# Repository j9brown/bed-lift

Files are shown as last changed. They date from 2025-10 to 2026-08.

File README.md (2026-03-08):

# Bed-lift controller

Controls a motorized bed-lift with two synchronized linear actuators for vertical lifting and lowering and two pairs of synchronized stepper motors for horizontal extension and retraction.  It fits in the back of a campervan.

## Circuit board revisions

Refer to the following documents for design synopsis, schematics, and circuit board illustrations.

- [v1](./hardware/v1/design-and-errata.md): Fixed errata, improved assignment of pin functions, added span limit hall sensors, buzzer and ESD protection
- [v0.2](./hardware/v0.2/design-and-errata.md): First feature-complete circuit board
- [v0.1](./hardware/v0.1/design-and-errata.md): Initial hand-assembled prototype

## About the "forklift" bed

This custom motorized bed fits in the back of a small campervan to allow dual-use of the living area in a standard wheelbase vehicle.  In its raised position, the bed platform is only supported from the back which gives it the appearance of a pallet on a forklift, hence the name.

To maximize space efficiency, the bed is designed for sleeping crosswise with the head and feet towards the sides of the vehicle.  This choice of sleeping orientation poses unique engineering challenges; it is more common to design lifting beds for sleeping lengthwise with the head and feet towards the front and back of the vehicle.

Because the van is narrower at roof elevantion than at sleeping elevation, the bed extends and retracts to span the gap between the main body of the bed platform and the sides of the vehicle.  The parts that extend and retract are called the bed wings (aka. wing spans).  The bed mattress is made of three cushions: one large central cushion on the main body of the bed platform and two narrower cushions that rest on the two bed wings.  The narrower cushions are removed and stowed on top of the bed before retracting the bed wings.

- When the bed is raised, the bed wings retract into the bed platform and the platform is cantilevered from steel columns attached to the rear doorframe and floor of the vehicle.

- When the bed is lowered, the bed wings extend from the bed platform and rest upon reinforced windowsills to transfer the load of the occupants to the vehicle walls.

The bed has limited load bearing capacity while raised so it must be lowered when occupied or while driving to prevent excess torque through the cantilever.  As an advantage, there are no cables, straps, bulkheads, guides, posts, or other obstructions in the front of the living area to support the bed.  As a disadvantage, the bed structure is heavy and difficult to build.

Feel free to contact me for advice if you are interested in building a bed like mine (and be prepared for a challenge)!

[Video tour of the v0.2 prototype](https://vimeo.com/1154513482/b7c7d3c8f7)

<details>
<summary>Photos of v0.2 prototype</summary>

### Bed lift in lowered position viewed from outside
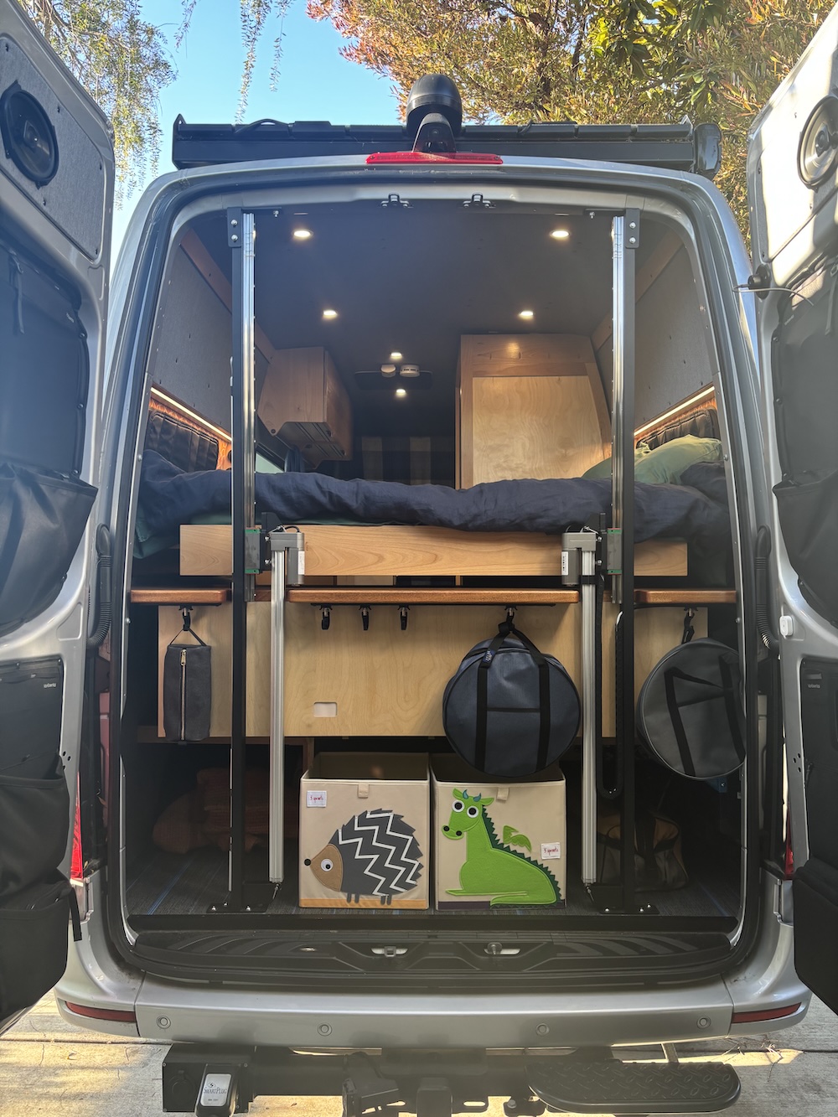
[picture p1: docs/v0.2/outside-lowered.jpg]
Bed lift in lowered position viewed from outside


### Bed lift in raised position viewed from outside
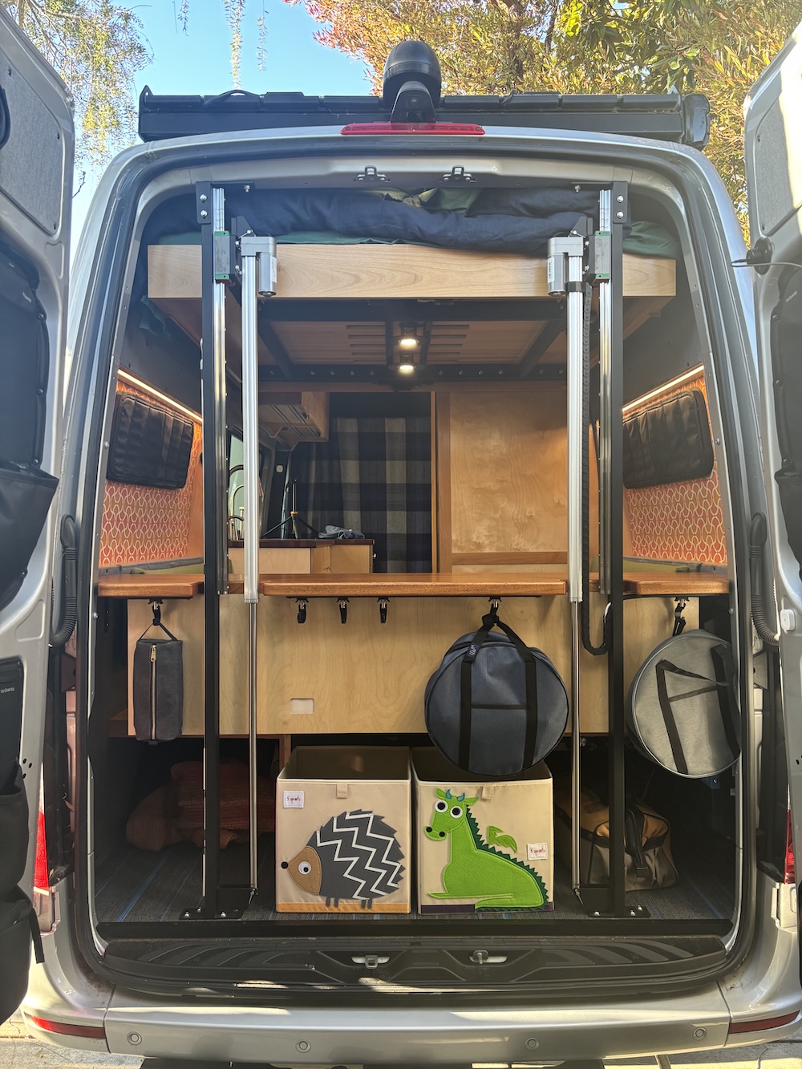
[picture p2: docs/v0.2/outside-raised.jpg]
Bed lift in raised position viewed from outside


### Bed lift in lowered position viewed from inside
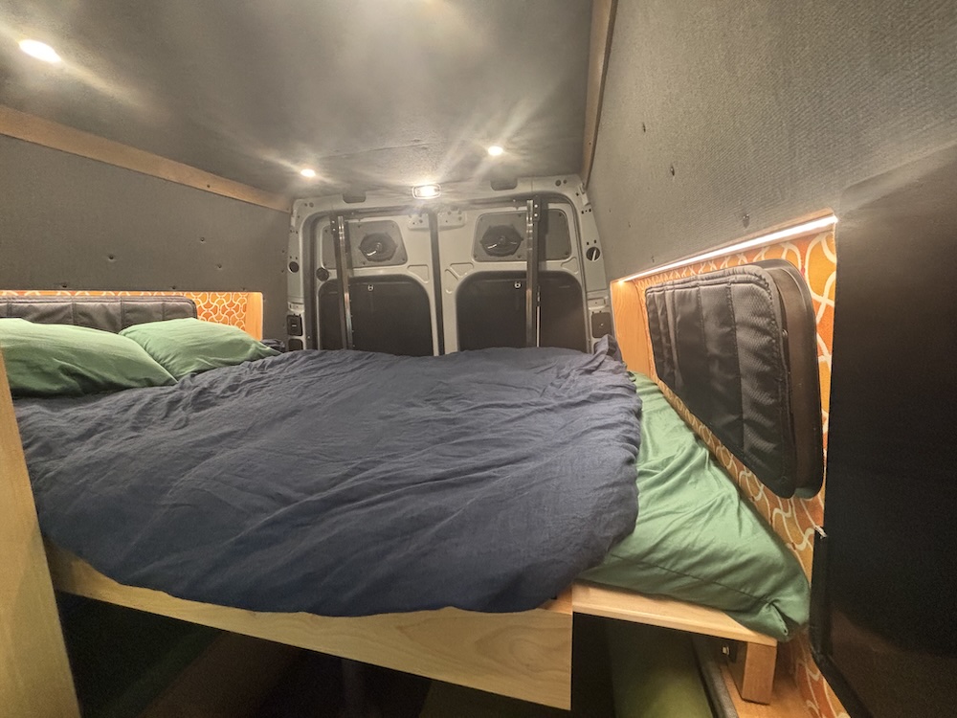
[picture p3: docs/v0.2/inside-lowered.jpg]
Bed lift in lowered position viewed from inside


### Bed lift in raised position viewed from inside
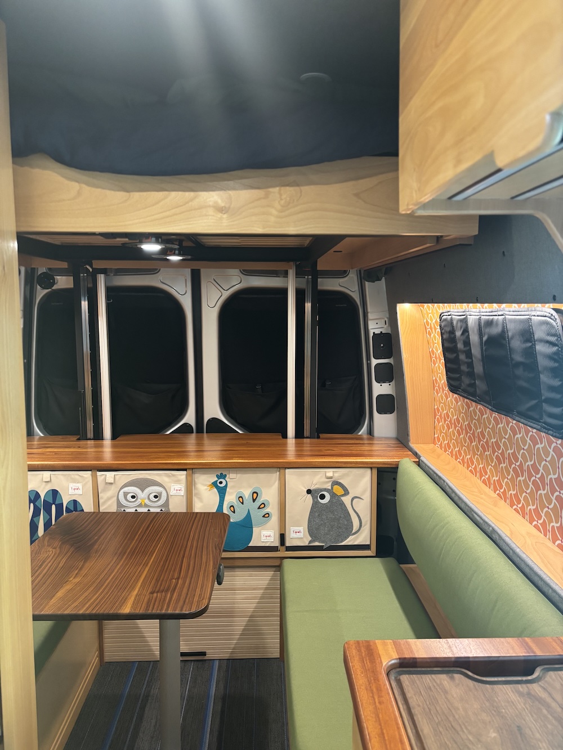
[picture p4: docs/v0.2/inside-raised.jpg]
Bed lift in raised position viewed from inside


### Bed lift controls
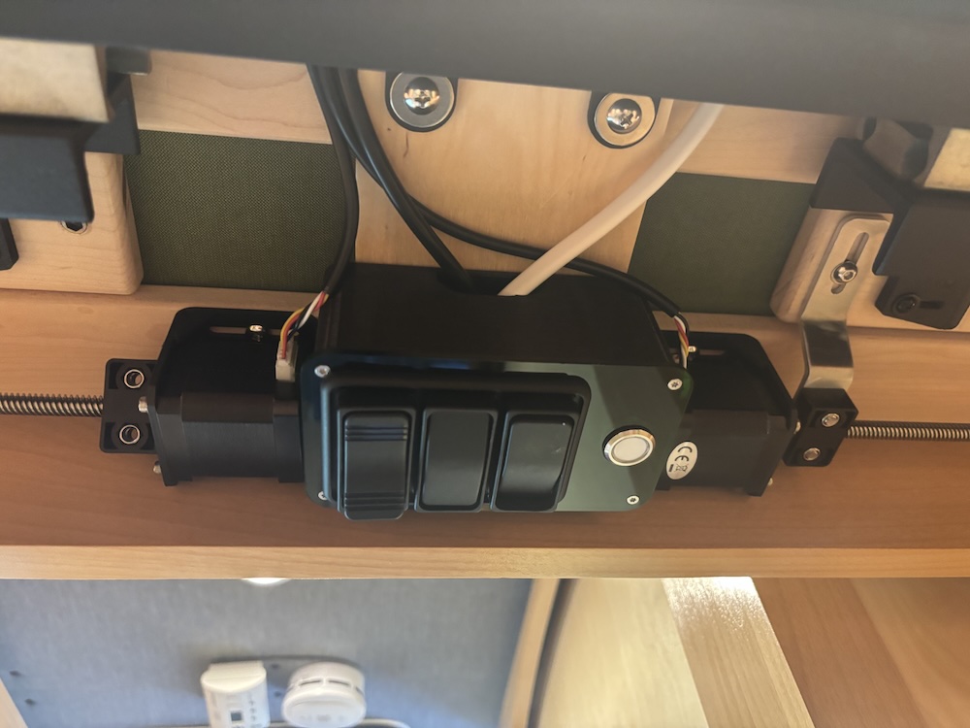
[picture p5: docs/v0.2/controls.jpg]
Bed lift controls


### Bed lift driver
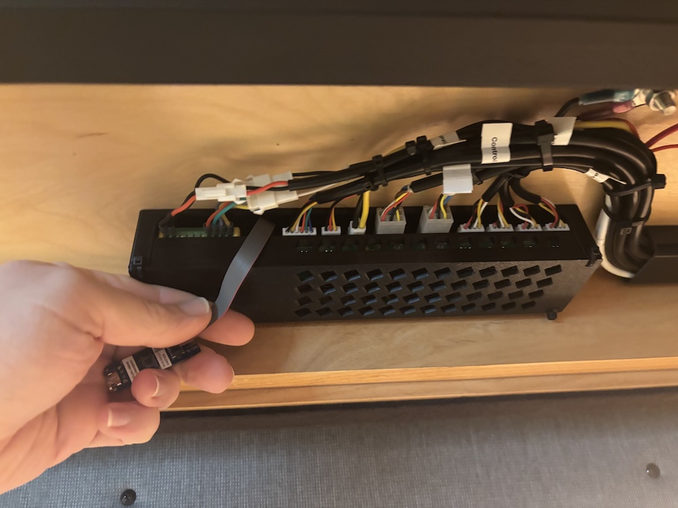
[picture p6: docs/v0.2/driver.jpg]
Bed lift driver


### Bed lift position encoder
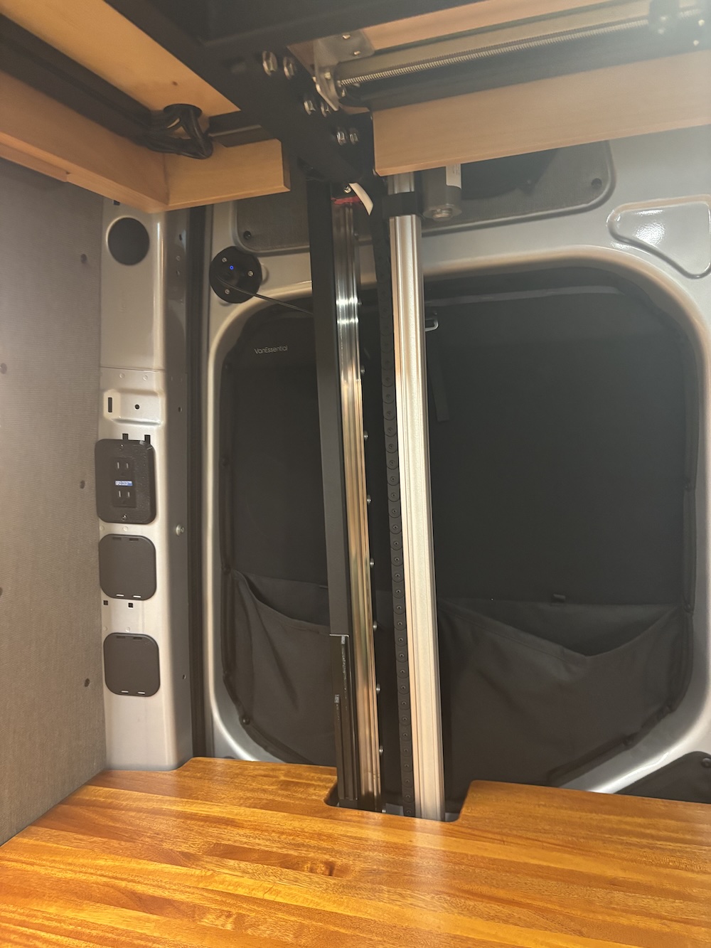
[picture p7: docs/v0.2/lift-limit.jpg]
Bed lift driver


</details>

<details>
<summary>Photos of v0.1 prototype</summary>

### Bed lift in lowered position
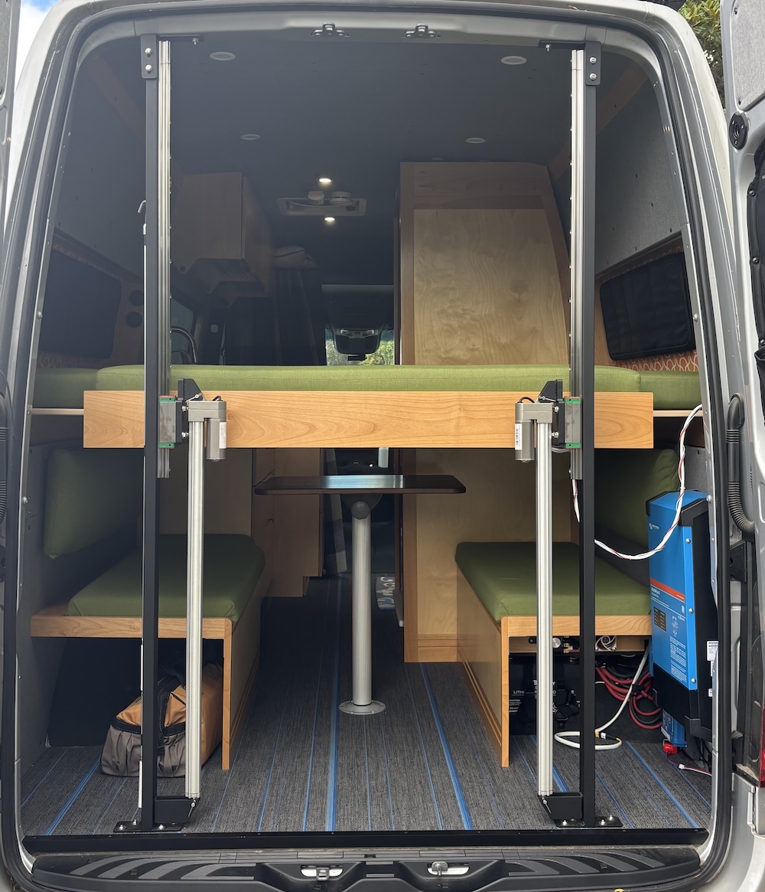
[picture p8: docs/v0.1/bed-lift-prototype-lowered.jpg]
Bed lift in lowered position


### Bed lift in raised position
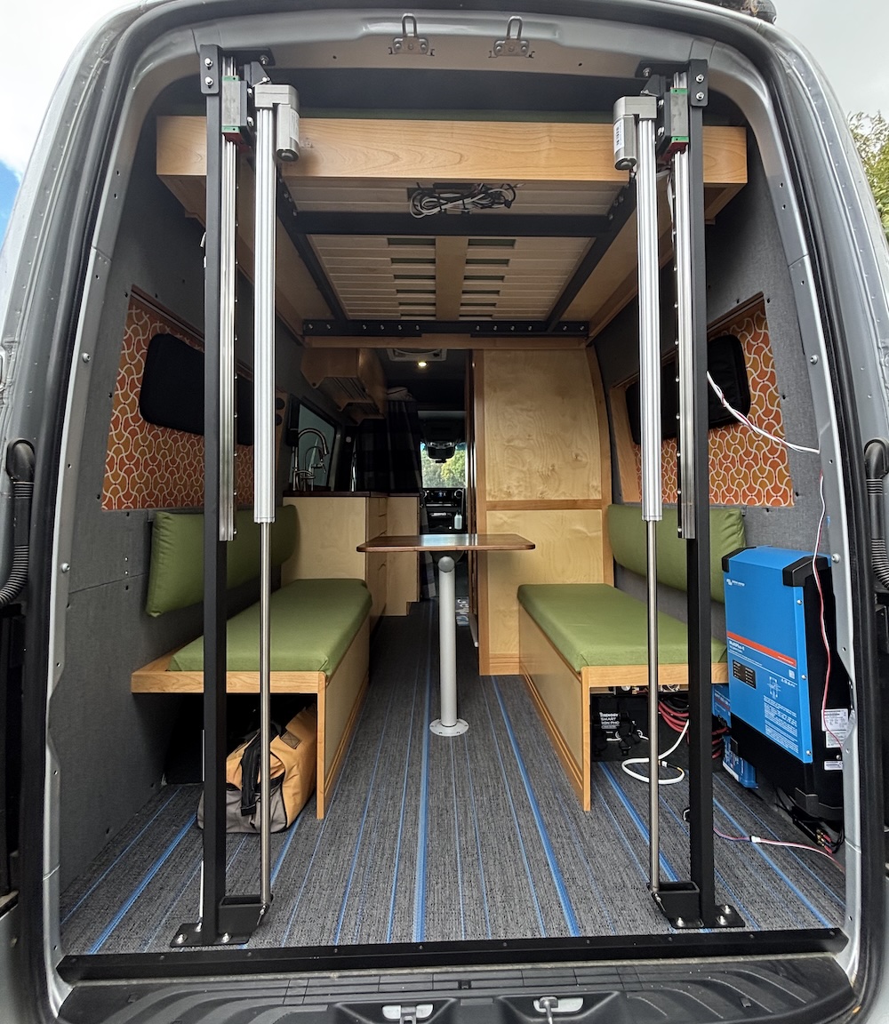
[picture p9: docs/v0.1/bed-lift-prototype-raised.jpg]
Bed lift in raised position


</details>

<details>
<summary>CAD model</summary>

### Bed lift in lowered position
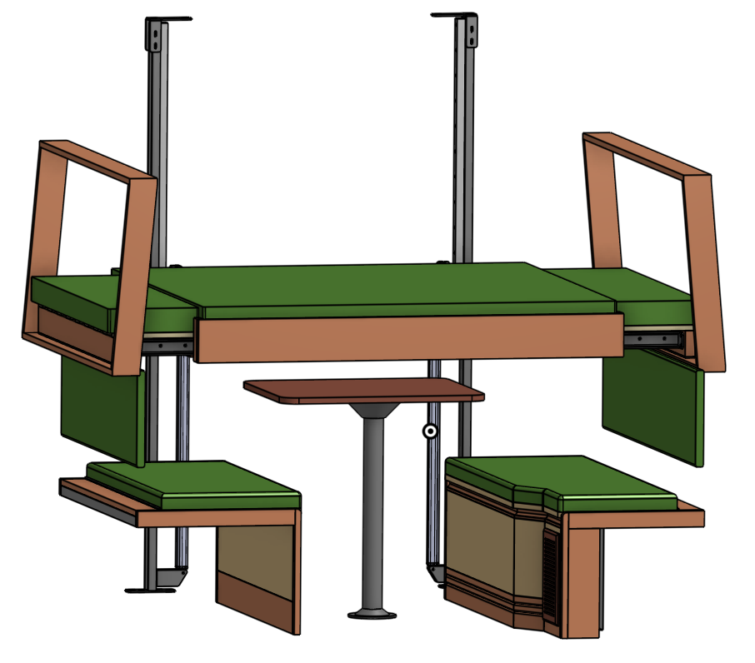
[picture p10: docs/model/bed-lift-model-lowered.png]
Bed lift in lowered position


### Bed lift in raised position
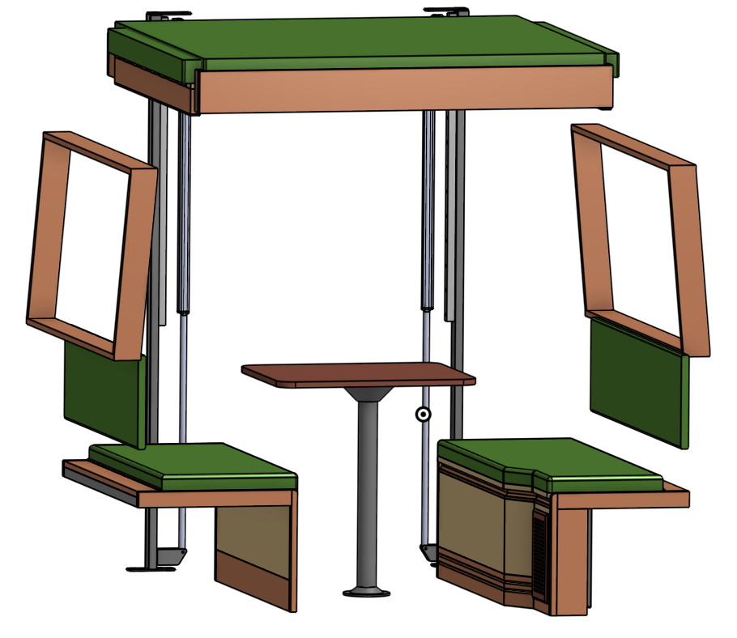
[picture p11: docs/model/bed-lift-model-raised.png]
Bed lift in raised position


</details>

## How to build the firmware

The firmware is based on Zephyr RTOS v4.3 and compiled with `west`.

1. Install the Zephyr RTOS SDK tools.  You can either follow the [Zephyr Getting Started Guide](https://docs.zephyrproject.org/latest/develop/getting_started/index.html) or install an extension for your IDE, such as [Zephyr IDE](https://zephyr-ide.mylonics.com/) or [Workbench for Zephyr](https://z-workbench.com/), that can install the tools for you.

2. Install the [xPack OpenOCD](https://xpack-dev-tools.github.io/openocd-xpack/docs/install/) package for your OS and add it to your system `PATH`.  This step is needed because the version of OpenOCD that is distributed with Zephyr is too old and doesn't support the STM32C0x series of chips.  We need OpenOCD v0.12.0-7 at minimum.

3. Get the code and its dependencies.  This is a little more complicated than simply cloning this git repository because the Zephyr `west` multi-tool assumes that all of the code resides within a top directory called a workspace.  You will need to create an empty directory to be the workspace first.  Here's how to do it from the command-line and the same thing can be done with IDE extensions.

```sh
$ mkdir bed-lift-workspace
$ cd bed-lift-workspace
$ west init -m https://github.com/j9brown/bed-lift
$ west update
```

4. Build and the firmware (either release or debug).

```sh
$ cd bed-lift/firmware/app
$ west build -p -d build/release
$ west build -p -d build/debug -- -DFEATURE_LOG=y -DFEATURE_DEBUG=y
```

5. Connect an ST-Link v3 programmer to the `DEBUG` port with an `STDC14` cable.  Flash the firmware.

```sh
$ cd bed-lift/firmware/app
$ west flash
```

Firmware for the older prototypes is preserved in the git history.

- The v0.2 firmware was based on Zephyr RTOS v4.2.1 and compiled with Platform IO.
- The v0.1 firmware was based on Arduino and compiled with Platform IO.

## Usage

The lift control panel has three switches:

- `Power`: This on / off switch provides power to the lift driver and all actuators.  It is intended to remain on indefinitely.  Can be used to cut power in case of emergencies.
- `Up / Off / Down`: This momentary-on / off / momentary-on switch has two positions.  Toggling the switch to the `Up` position raises the lift to the lounge position.  Toggling the switch to the `Down` position lowers the lift to the sleeping position.  The switch must be held in the `Up` or `Down` position for 0.5 seconds to engage the actuators as a precaution against accidental triggering.  The lift stops moving immediately as soon as the switch is released and returns to the `Off` position.
- `Mode`: This momentary-on / off switch activates special modes.

By default, the lift starts on the `Main Menu` and the `Up / Off / Down` controls whether the lift moves into the lounge or sleep position.

While holding the switch `Up` or `Down` and the lift is raising or lowering, press the `Mode` button to activate automatic movement.  Then, release all of the controls and the lift will continue moving in the requested direction until the final position is reached or an error occurs.  To stop automatic movement, press any control.

**Use caution when activating automatic movement and continue paying attention to the lift to avoid damage or injury!**

to ensure the lift won't encounter any obstructions in this mode because it could damage itself if you aren't paying attention!

To access a different menu, press and hold the `Mode` button for 3 seconds until the indicator lights `Amber` then blinks one or more times in a different color and a tone is played.  The second color indicates the menu and the number of blinks indicates the action that will be performed when the `Up / Off / Down` switch is activated.  Press the `Mode` button to cycle among actions and observe the number of blinks change.  Press and hold the `Mode` button for 0.5 seconds to access the next menu and observe the blink color change.  Refer to the table below to identify the currently selected menu action.

The lift reverts to an idle state when the user does not interact with the controls for some time.

### Visual feedback

An RGB color indicator shows the state of the device at the control panel.  There is also a monochromatic red LED on the circuit board itself that indicators the same state as the indicator (but without color).

- When the lift remains idle for some time, the indicator turns off.
- When the lift is rising, the indicator shows a rainbow color wheel cycling from red to violet.
- When the lift is lowering, the indicator shows a rainbow color wheel cycling from violet to red.
- When the lift achieves the lounge or sleep position, the indicator lights `Green`.
- When the lift movement is aborted without achieving the lounge or sleep position, the indicator lights `Amber`.
- When a diagnostic menu mode is active, the indicator lights `Amber` then blinks one or more times in a different color depending on the menu.
- When an error occurs, the indicator lights `Red` then blinks one or more times in a different color depending on the error.

| Solid color  | Blink color  | Blinks | Purpose  | Meaning |
| --- | --- | --- | --- | --- |
| Rainbow up | | | Activity | Lift is rising |
| Rainbow down | | | Activity | Lift is lowering |
| Green | | | Status | Lift is in lounge or sleep position, ready for use |
| Amber | | | Status | Lift is in an intermediate position, not ready for use |
| Amber | Cyan | 1 | Menu | Lift menu: Jog both lift actuators in tandem (synchronized) |
| Amber | Cyan | 2 | Menu | Lift menu: Jog both lift actuators indepedently (not synchronized) |
| Amber | Cyan | 3 | Menu | Lift menu: Jog lift actuator 1 (driver side) |
| Amber | Cyan | 4 | Menu | Lift menu: Jog lift actuator 2 (passenger side) |
| Amber | Blue | 1 | Menu | Span menu: Jog all span actuators in tandem (synchronized) |
| Amber | Blue | 2 | Menu | Span menu: Jog both span actuators 1 and 2 (driver side) in tandem (synchronized) |
| Amber | Blue | 3 | Menu | Span menu: Jog both span actuators 3 and 4 (passenger side) in tandem (synchronized) |
| Amber | Blue | 4 | Menu | Span menu: Jog both span actuator 1 (front driver side) independently (not synchronized) |
| Amber | Blue | 5 | Menu | Span menu: Jog both span actuator 2 (rear driver side) independently (not synchronized) |
| Amber | Blue | 6 | Menu | Span menu: Jog both span actuator 3 (front passenger side) independently (not synchronized) |
| Amber | Blue | 7 | Menu | Span menu: Jog both span actuator 4 (rear passenger side) independently (not synchronized) |
| Red | | | Error | Error: An unspecified error occurred |
| Red | Magenta | 1 | Error | Control error: Movement of the bed has been remotely inhibited |
| Red | Amber | 1 | Error | Bed error: The bed components are in an unknown or unexpected state |
| Red | Cyan | 1 | Error | Lift error: Motor driver reported a fault |
| Red | Cyan | 2 | Error | Lift error: The actuators lost synchronization |
| Red | Cyan | 3 | Error | Lift error: Lift stationary when it should be moving or the hall sensors are not working correctly |
| Red | Cyan | 1 | Error | Lift error: I/O error communicating with the motor driver |
| Red | Cyan | 1 | Error | Lift error: Operation timed out because poll wasn't called often enough |
| Red | Blue | 1 | Error | Span error: Motor driver reported a fault |
| Red | Blue | 2 | Error | Span error: The actuators lost synchronization |
| Red | Blue | 3 | Error | Span error: The actuators did not stall at their home position as expected |
| Red | Blue | 4 | Error | Span error: The actuators traveled further than the expected distance without stalling |
| Red | Blue | 5 | Error | Span error: I/O error communicating with the motor driver |
| Red | Blue | 6 | Error | Span error: Operation timed out because poll wasn't called often enough |

### Audible feedback

A piezo buzzer provides audible feedback.

- When the lift successfully raises into the lounge position, it plays a brief fanfare that ends on a rising tone.
- When the lift successfully lowers into the sleep position, it plays a brief fanfare that ends on a falling tone.
- When the lift encounters an error, it plays three long tones as an alert.
- When the user attempts to perform an action that has been remotely inhibited, the lift plays three quick tones.
- When using the diagnostic menu, the lift plays a tone as each menu or mode is entered.

### I2C interface

Connect an I2C host to the lift driver's `EXT I2C` port using a `QWIIC` connector to remotely monitor the device, remotely inhibit operation of the control panel, and access low-level debug and test features.  The `EXT I2C` port galvanically isolates the bed lift from the host's power supply for safety.

Refer to [monitor.c](./firmware/app/src/monitor.c) for the I2C protocol implementation.

## Notice

The bed-lift software, documentation, design, and all copyright protected artifacts are released under the terms of the [MIT license](LICENSE).

The bed-lift hardware is released under the terms of the [CERN-OHL-W license](hardware/LICENSE).

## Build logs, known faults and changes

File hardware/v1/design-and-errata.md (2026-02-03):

# Bed lift v1.0

**Status: Fabricated, tested, in service, no issues found**

## Design synopsis

The controller has the following major components:

- [STM32C051C8T6](https://www.st.com/resource/en/datasheet/stm32c051c8.pdf) with 64 KB flash and 12 KB RAM controls the actuators. It is programmed with SWD using a STDC14 connector. The timer peripherals are used extensively for motor control and feedback.
- [ISO1640](https://www.ti.com/lit/ds/symlink/iso1640.pdf) isolates the I2C bus to prevent ground loops through the `EXT I2C` connector because the driver has a separate power supply.
- Four [DRV8434S](https://www.ti.com/lit/ds/symlink/drv8434s.pdf) stepper motor drivers operate the four motors that extend and retract the side spans of the bed.
- Two [DRV8874](https://www.ti.com/lit/ds/slvsf66a/slvsf66a.pdf) motor drivers operate the two linear actuators that raise and lower the bed.
- [LP2985-33](http://www.ti.com/lit/ds/symlink/lp2985.pdf) LDO powers the logic circuits at 3.3 V
- [LP2985-50](http://www.ti.com/lit/ds/symlink/lp2985.pdf) LDO powers the hall sensors at 5.0 V
- [PS1240P02BT](https://product.tdk.com/en/system/files/dam/doc/product/sw_piezo/sw_piezo/piezo-buzzer/catalog/piezoelectronic_buzzer_ps_en.pdf) buzzer provides audible feedback
- Circuit protection elements
  - Supply: TVS
  - Actuators: overcurrent, stall-detection, open-load, short-circuit
  - Switch inputs: ESD diodes
  - External I2C bus: galvanic isolation, hot plug

The device receives user control input from a momentary rocker switch attached to the `CONTROL` input and it provides feedback on its progress with an RGB LED indicator and piezo buzzer. To synchronize the motors and move the bed lift into the correct pose, the device receives position feedback from the `LIFT` actuator hall sensors, `LIFT LIMIT` switches, `SPAN LIMIT` hall sensors, and stepper motor driver stall detection. It can also be monitored and controlled remotely by an external I2C host via the `EXT I2C` connector.

The `EXPANSION` and `INT I2C` interfaces expose additional signals for future use.

The circuit board requires a 12 V DC nominal supply protected by a 10 A external fuse.

The schematics include the BOM and metadata for the JLCPCB fabrication toolkit plug-in.

## Illustrations

[Schematics PDF](bed-lift.pdf)

### PCB front
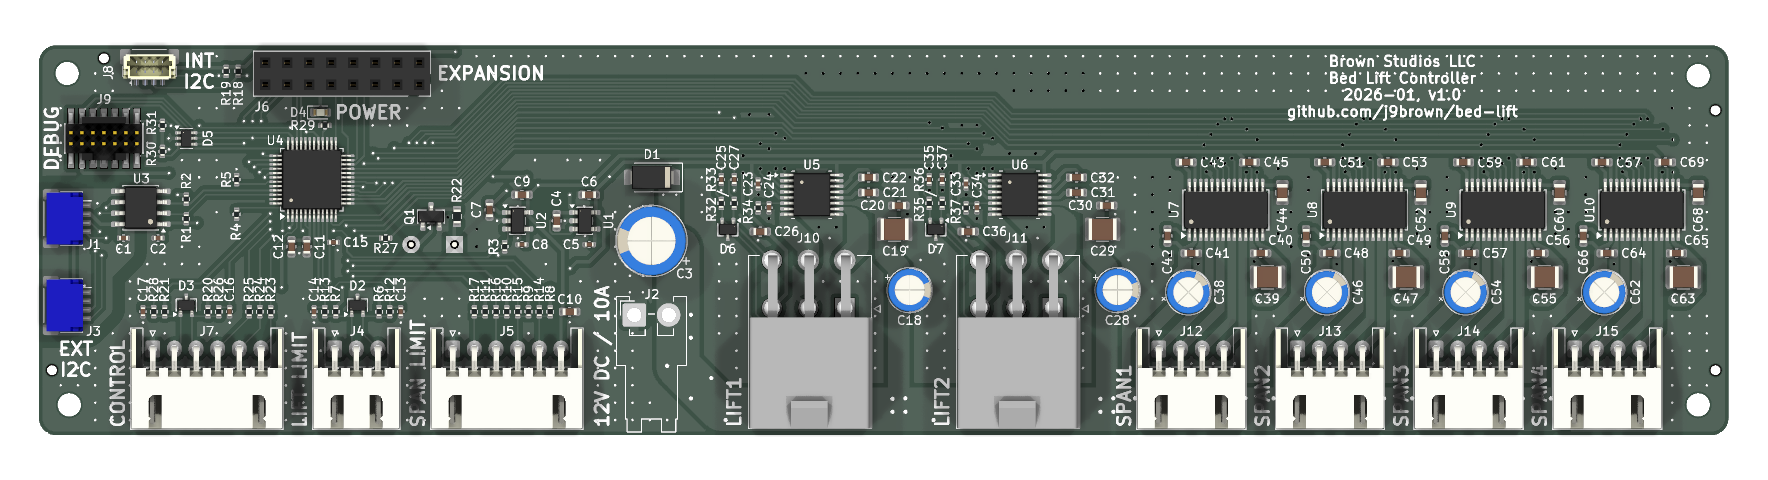
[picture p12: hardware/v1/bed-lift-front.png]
PCB front


### PCB back
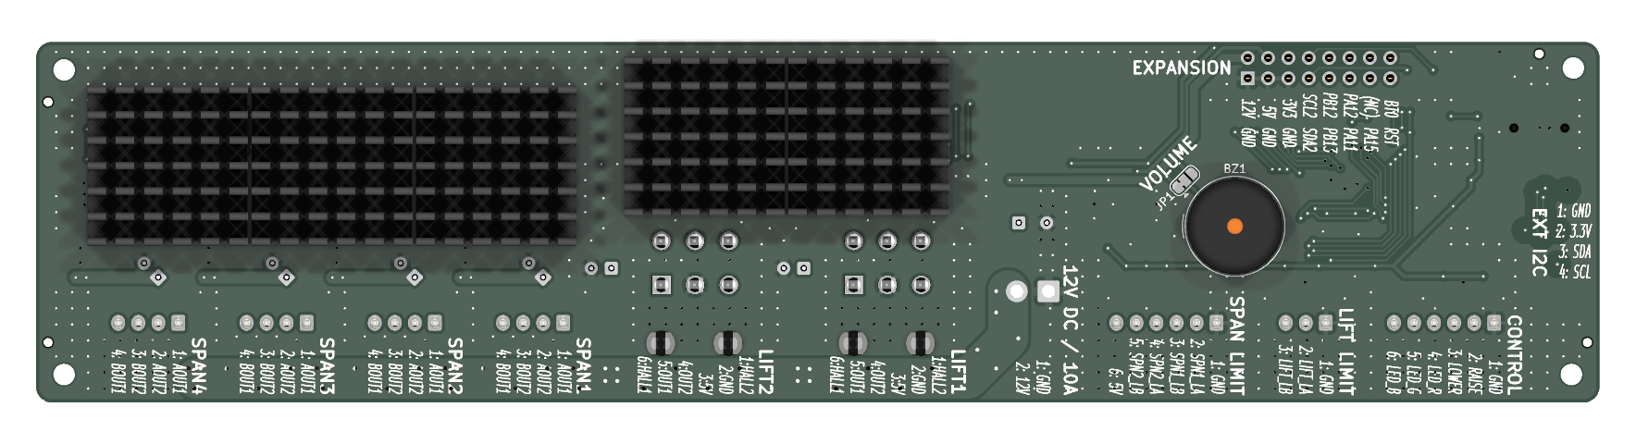
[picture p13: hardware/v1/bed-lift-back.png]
PCB back


## Fabrication

Use the `JLCPCB fabrication toolkit` plug-in to generate files for JLCPCB.

Fabrication parameters:

- Material: 4 layers, FR4 TG155, ENIG, 1 oz outer copper, 0.5 oz inner copper
- Via covering: plugged
- Min via hole size: 0.3 mm (default)
- Board outline tolerance: 0.2 mm (default)
- Assembly side: top
- Tooling holes: by customer
- Parts selection: by customer
- Solder paste: high temp (default)

Because the piezo buzzer is the only component on the back side, it may be cheaper to solder it manually after manufacture.

## Additional materials

Control panel switches

  - 3 gang switch panel mount
    - Carling Technologies VM3-01
  - Up/down control
    - Carling Technologies V8D2S001-00000-000 Contura momentary on/off/on rocker switch
    - Carling Technologies VVJZZ00-000 Contura XII paddle actuator
  - Mode control
    - Carling Technologies V2D2S001-00000-000 Contura momentary on/off rocker switch
    - Carling Technologies VV6ZZ00-000 Contura XI recessed actuator
  - Arm/disarm control
    - Carling Technologies V1D2S001-00000-000 Contura maintained on/off rocker switch
    - Carling Technologies VV1ZZ00-000 Contura X raised actuator
  - Generic small signal diodes to connect the mode switch to both up/down inputs

Control panel indicators

  - 3 V RGB panel indicator
    - Dialight 6251121307F or 6201121117F

Lift position encoders

  - 2 generic normally open lever arm micro limit switches with rollers

Span position encoders

  - 4 Littelfuse 55100-3M-02-A

Heat sinks

  - 5 generic 20 mm L x 20 mm W x 10 mm H self-adhesive heatsinks mounted on back side underneath the motor drivers

Actuators

  - 2 [Progressive Automation PA-09-03-30](https://www.progressiveautomations.com/products/mini-medium-force-linear-actuator) linear actuators for the lift, rated for 4 A peak at maximum 330 lbs load, hall sensor produces 660 pulses per inch of travel
  - 4 [Stepper Online 17E19S1684MB4-300RS](https://www.omc-stepperonline.com/nema-17-external-acme-linear-stepper-motor-1-68a-48mm-stack-screw-lead-8mm-0-31496-lead-length-300mm-17e19s1684mb4-300rs) stepper motors for the spans, rated for 1.68 A rms per phase

## Lift position encoders

Install two limit switches on the bed frame.  Each limit switch has a lever arm that is depressed when it rolls over a raised 3D printed plastic strip attached to the face of one of the bed lift columns.  Together the limit switches encode the position of the bed.

| State | Position | `Limit A` | `Limit B` | Wing action |
| ----- | --- | --- | --- | --- |
| `1` | Maximum elevation | `ON` | `OFF` | Fully retracted |
| `2` | Above safe zone | `OFF` | `OFF` | Fully retracted |
| `3` | Within safe zone | `OFF` | `ON` | Extending/retracting |
| `4` | Below safe zone | `ON` | `ON` | Fully extended |

To raise the bed...

  - state `4`: raise platform
  - state `3`: retract wings then raise platform (can do both simultaneously)
  - state `2`: retract wings then raise platform
  - state `1`:
    - if full range of travel permitted (no cushions or other bulky materials stored on the bed) then raise platform until end-of-travel
    - otherwise stop

To lower the bed...

  - state `1`: lower platform
  - state `2`: lower platform
  - state `3`: extend wings then lower platform (can do both simultaneously)
  - state `4`:
    - if wings fully extended then lower platform until end-of-travel
    - otherwise: raise platform until state `3` achieved and the wings can be extended

## Span hall sensors

Install one hall sensor at each of the end-of-travel of the rear span actuators on both sides for a total of 4 sensors.

Although end-of-travel can be determined by observing stepper motor stalls, the motor can stall in mid-travel when it encounters sufficient resistance.  The span limit switches let the lift confirm the position before continuing the movement to the next pose.

## Pin function map

### Debug

- NRST on PF2: RESET
- SWDIO on PA13: SWDIO, serial wire data, internal pull-up activated on reset
- SWCLK/BOOT0 on PA14: SWCLK/BOOT0, serial wire clock, internal pull-down activated on reset

### Console

- USART1_TX on PA9: CONSOLE_TX, serial TX
- USART1_RX on PA10: CONSOLE_RX, serial RX

### External I2C bus (receives commands as target)

- I2C1_SCL on PB6: EXT_I2C_SCL, serial clock
- I2C1_SDA on PB7: EXT_I2C_SDA, serial data 

### Internal I2C bus (reserved for use as controller)

- I2C2_SCL on PB10: INT_I2C_SCL, serial clock
- I2C2_SDA on PB11: INT_I2C_SDA, serial data 

### SPI bus

- SPI1_NSS on PA4: SPAN_SCS, serial chip select
- SPI1_SCK on PA5: SPAN_SCLK, serial clock
- SPI1_MISO on PA6: SPAN_SDI, serial data in
- SPI1_MOSI on PA7: SPAN_SDO, serial data out

### Lift actuators

#### Driver interface

- TIM1_CH1 on PA0: LIFT1_IN1, PWM output
- TIM1_CH2 on PA1: LIFT1_IN2, PWM output
- TIM1_CH3 on PA2: LIFT2_IN1, PWM output
- TIM1_CH4 on PA3: LIFT2_IN2, PWM output
- TIM1_BKIN2 on PC14: LIFT_FAULT, trigger TIM1 break input 2, active low
- GPIO on PC13: LIFT_SLEEP, active low

The TIM1 break function prevents runaway motor operation when triggered by a system fault, debug mode, or TIM1_BKIN2 active.  Configured to stop both lift actuators when either one encounters a fault.

- DBG_TIM1_STOP freezes the counter during debugging.
- TIM1_BDTR:OSSI=1 forces outputs to inactive state on break.

#### Rotary encoders (digital hall sensors)

- GPIO on PB0 (EXTI0): LIFT1_HALL1, interrupt input, active high
- GPIO on PB1 (EXTI1): LIFT1_HALL2, interrupt input, active high
- GPIO on PB2 (EXTI2): LIFT2_HALL1, interrupt input, active high
- GPIO on PB3 (EXTI3): LIFT2_HALL2, interrupt input, active high

Quadrature decoding triggered by EXTI0-1 and EXTI2-3 interrupt with high-priority and not shared with any other I/O pins. We could have used TIM2 and TIM3 to decode both quadrature signals but we need one of those peripherals for the indicator PWM.

#### Position encoders (limit switches)

- GPIO on PF0: LIFT_LIMIT_A, active low
- GPIO on PF1: LIFT_LIMIT_B, active low

### Span actuators

#### Driver interface

- GPIO on PB4: SPAN_SLEEP, active low
- GPIO (or TIM16_BKIN) on PB5: SPAN_FAULT, active low
- TIM16_CH1 on PB8: SPAN_STEP, active high

The drivers are connected to the SPI bus in a daisy-chain. All drivers receive the same step pulse and the direction is specified via SPI.

The TIM16 break function prevents runaway motor operation when triggered by a system fault or debug mode.  Optionally could be configured to stop all span actuators on driver faults (although this hasn't been needed yet).

- DBG_TIM16_STOP freezes the counter during debugging.
- TIM16_BDTR:OSSI=1 forces outputs to inactive state on break.

#### Position encoders (digital hall sensors)

- GPIO on PD0: SPAN1_LIMIT_A, active low
- GPIO on PD1: SPAN1_LIMIT_B, active low
- GPIO on PD2: SPAN2_LIMIT_A, active low
- GPIO on PD3: SPAN2_LIMIT_B, active low

### Indicator LEDs

- TIM3_CH1 on PC6: LED_STATUS_R, PWM output, active high
- TIM3_CH2 on PC7: LED_STATUS_G, PWM output, active high
- TIM3_CH3 on PC15: LED_STATUS_B, PWM output, active high
- TIM3_CH4 on PA8: LED_POWER, PWM output, active low

### Control buttons

- GPIO on PB14 (EXTI14): CTRL_LOWER, interrupt input, active low
- GPIO on PB15 (EXTI15): CTRL_RAISE, interrupt input, active low

### 5 V LDO for hall sensors

- GPIO on PF3: 5V_EN, active high

The lift hall sensors require 5 V and do not operate reliably on 3.3 V.

The span hall sensors operate on 2.7 V to 24 V.  This design uses the 5 V LDO instead of 3.3 V so the sensors can be easily turned off to save power together with the lift hall sensors.

### Buzzer

- TIM17_CH1 on PB9: SOUND, active high

### Unused pins available for expansion

- PA11 (ADC_IN11)
- PA12 (ADC_IN12)
- PA15 (TIM2_CH1)
- PB12 (ADC_IN22, TIM1_BKIN)
- PB13 (---)

### [System bootloader](https://www.st.com/resource/en/application_note/an2606-stm32-microcontroller-system-memory-boot-mode-stmicroelectronics.pdf) configured pins

- Can access system bootloader via the console UART and external I2C ports by pulling BOOT0 high on reset
- Pull-up inputs: PA2, PA9
- Pull-up outputs: PA3, PA10, PB6, PB7, PB10, PB11
- Pull-down outputs: PA4, PA5, PA6, PA7, PB12, PB13, PB14, PB15

## Errata

None yet...

## Updates

### Major changes since v0.2

- Use an MCU variant with more pins and flash, expose unused pins to an expansion port.
- Use STDC14 connector for debugging instead of TagConnect to improve accessibility.
- Assign PWM capable outputs to motor driver inputs, drive the step signal with PWM, attach fault signals to break inputs.
- Correct the lift motor connector pins, provide 5 V for its hall sensors, attach hall sensor signals to EXTI0-4 lines for higher priority interrupt handling.
- Drive DRV8434S VREF with 3.3 V as recommended in the datasheet and provide missing SPI SCS signal.
- Improve switch input debouncing and add ESD protection.
- Add span limit hall sensor inputs to verify end-of-travel.
- Add a buzzer for audible feedback.
- Place additional bulk capacitance closer to every motor driver to distribute the switching current more evenly taking into account DC bias derating for the MLCC capacitors.
- Increase physical dimensions to allow for additional connectors and larger heat sinks. Keep the B.Cu plane mostly contiguous under the motor drivers to improve heat dissipation.
- Avoid burying fixed voltage signals under chips in case they need to be bodged like last time.

### Remarks

- Considered replacing the 3.3 V LDO with a buck converter but the idle current is already so low (should be less than 5 mA) that it's not worth the complexity.
- The RC filter for the lift hall sensors does not appear to be strictly necessary but it seems prudent given prior observations of sensor noise (which appears to have been resolved by increasing the supply to 5 V).  Set the filter cutoff below 20 kHz to filter out PWM noise.  The v0.2 design had the same filter and it worked fine and the signals looked clean so leaving it in.  Added ESD protection to protect the input pins.
- The extra bulk capacitance may increase leakage current. If it becomes a problem, some capacitors can always be removed.
- The via stitching pattern is generated with the `kicad-action-scripts` plug-in based on a 2 mm gap, 0.5 mm diameter, 0.3 mm hole.
- The schematics are plotted with dark theme `Arcana`.

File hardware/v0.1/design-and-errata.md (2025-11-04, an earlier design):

# Bed lift v0.1 (OBSOLETE)

**Status: Superseded by v0.2, see [errata](#errata)**

## Design synopsis

This initial prototype of the bed lift was built on protoboard with components on-hand.  It uses an RP2040 and two DRV8874 motor drivers to synchronize the movement of two linear actuators for lifting the bed.  It lacks servo drivers to extend the bed sideways.

## Illustrations

[Schematics PDF](bed-lift.pdf)

## Errata

This design is difficult to assemble and not intended to be replicated by others.

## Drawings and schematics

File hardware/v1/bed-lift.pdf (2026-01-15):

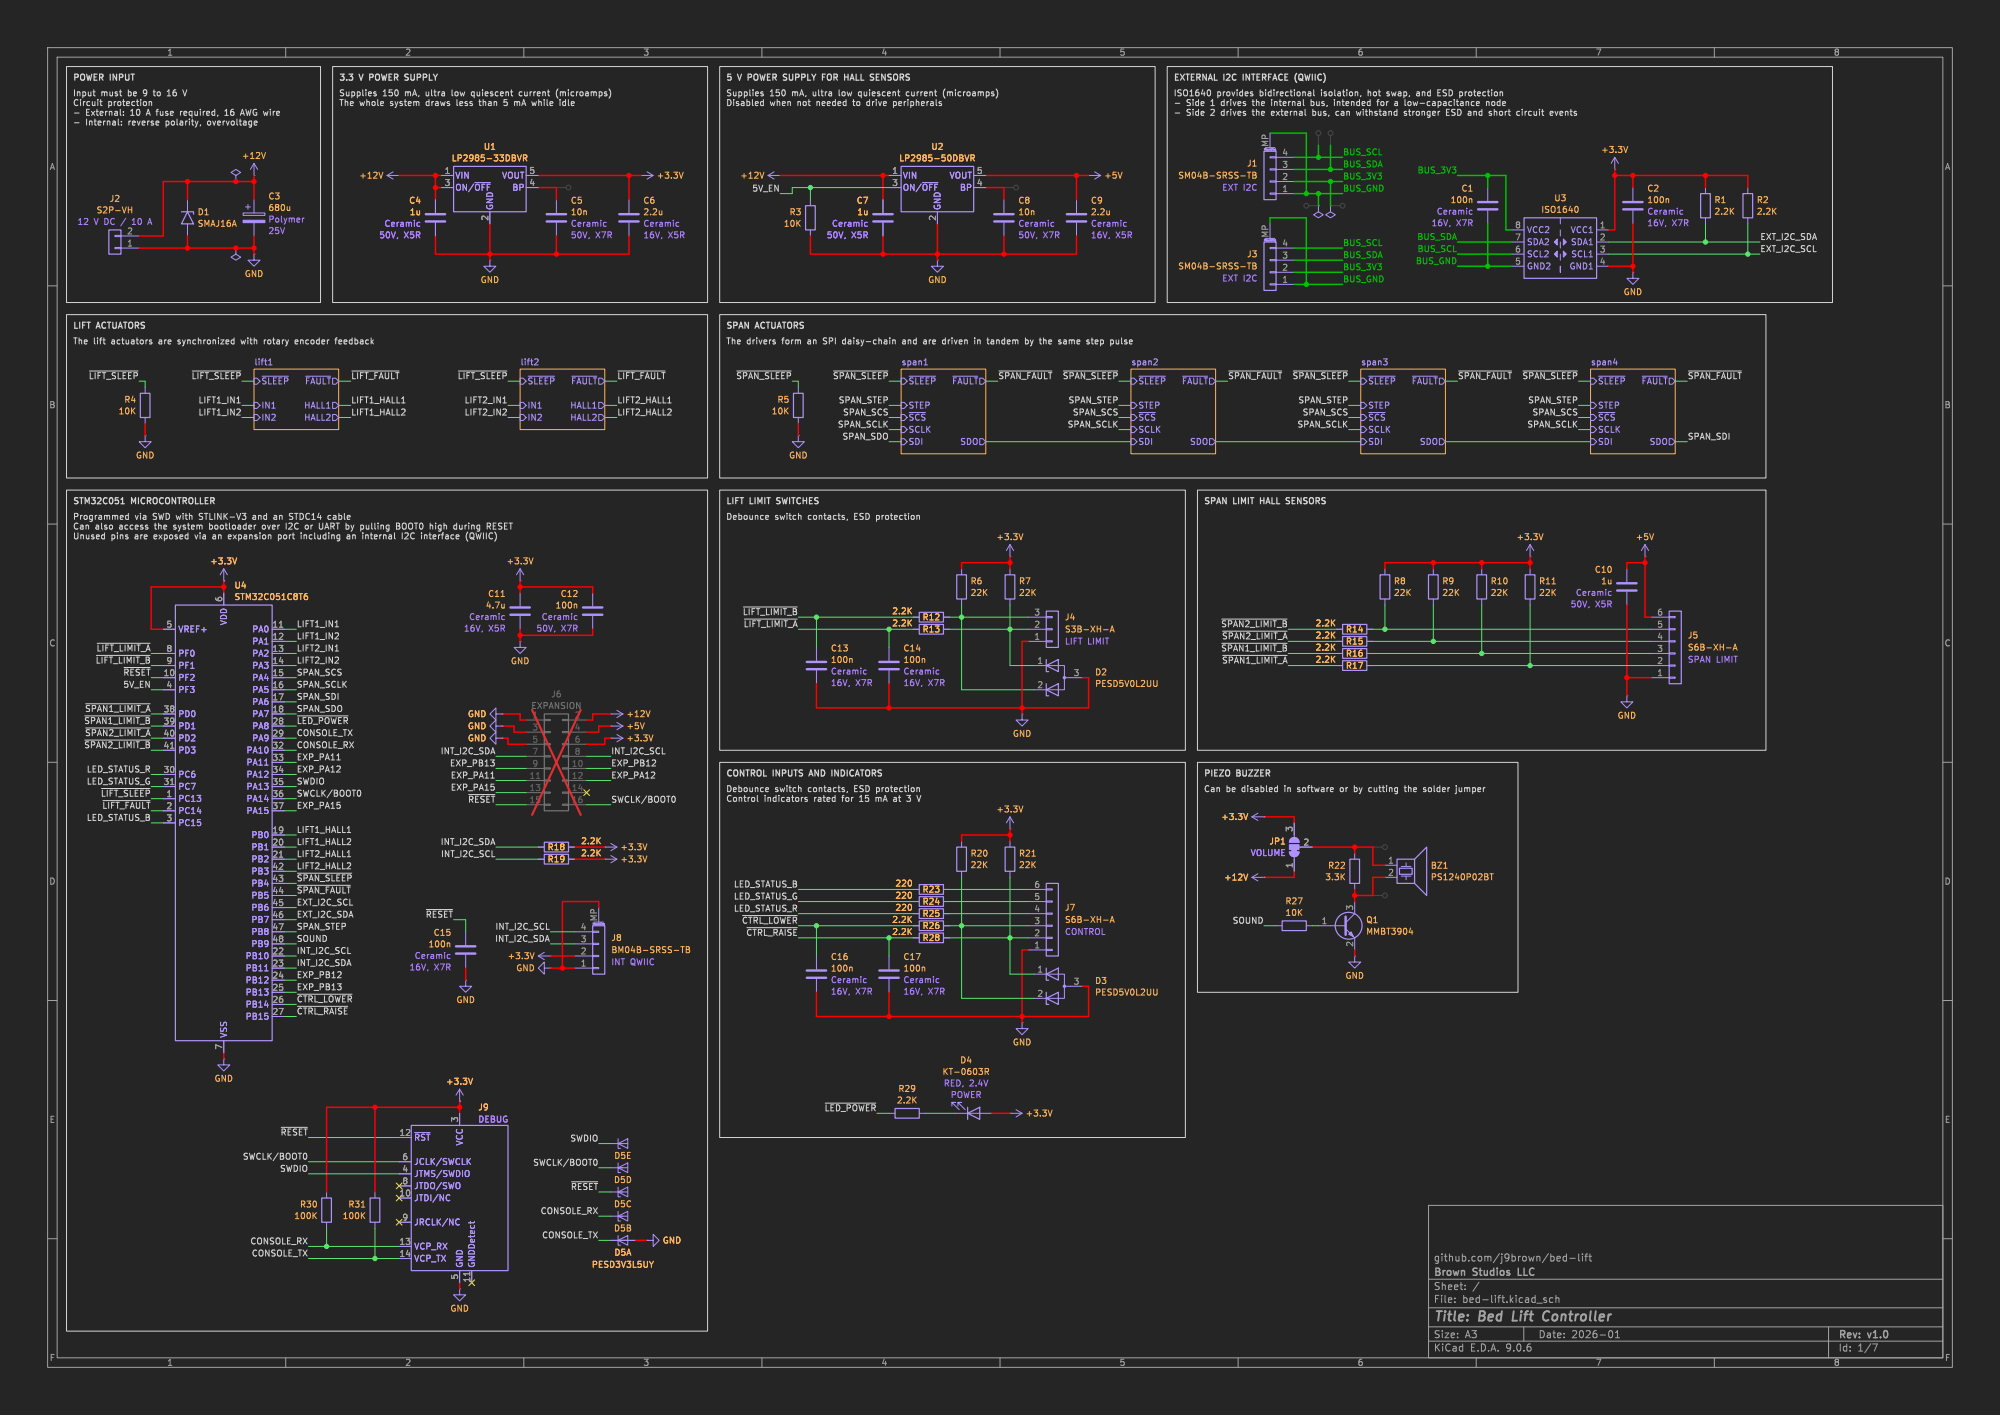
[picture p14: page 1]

Input must be 9 to 16 V Circuit protection

2 VOUT 5 BP 4 +3.3V GND GND GND

4.7u Ceramic 16V, X5R GND GND GND GND

+3.3V GND
INT QWIIC GNDDetect 11 VCC

github.com/j9brown/bed-lift

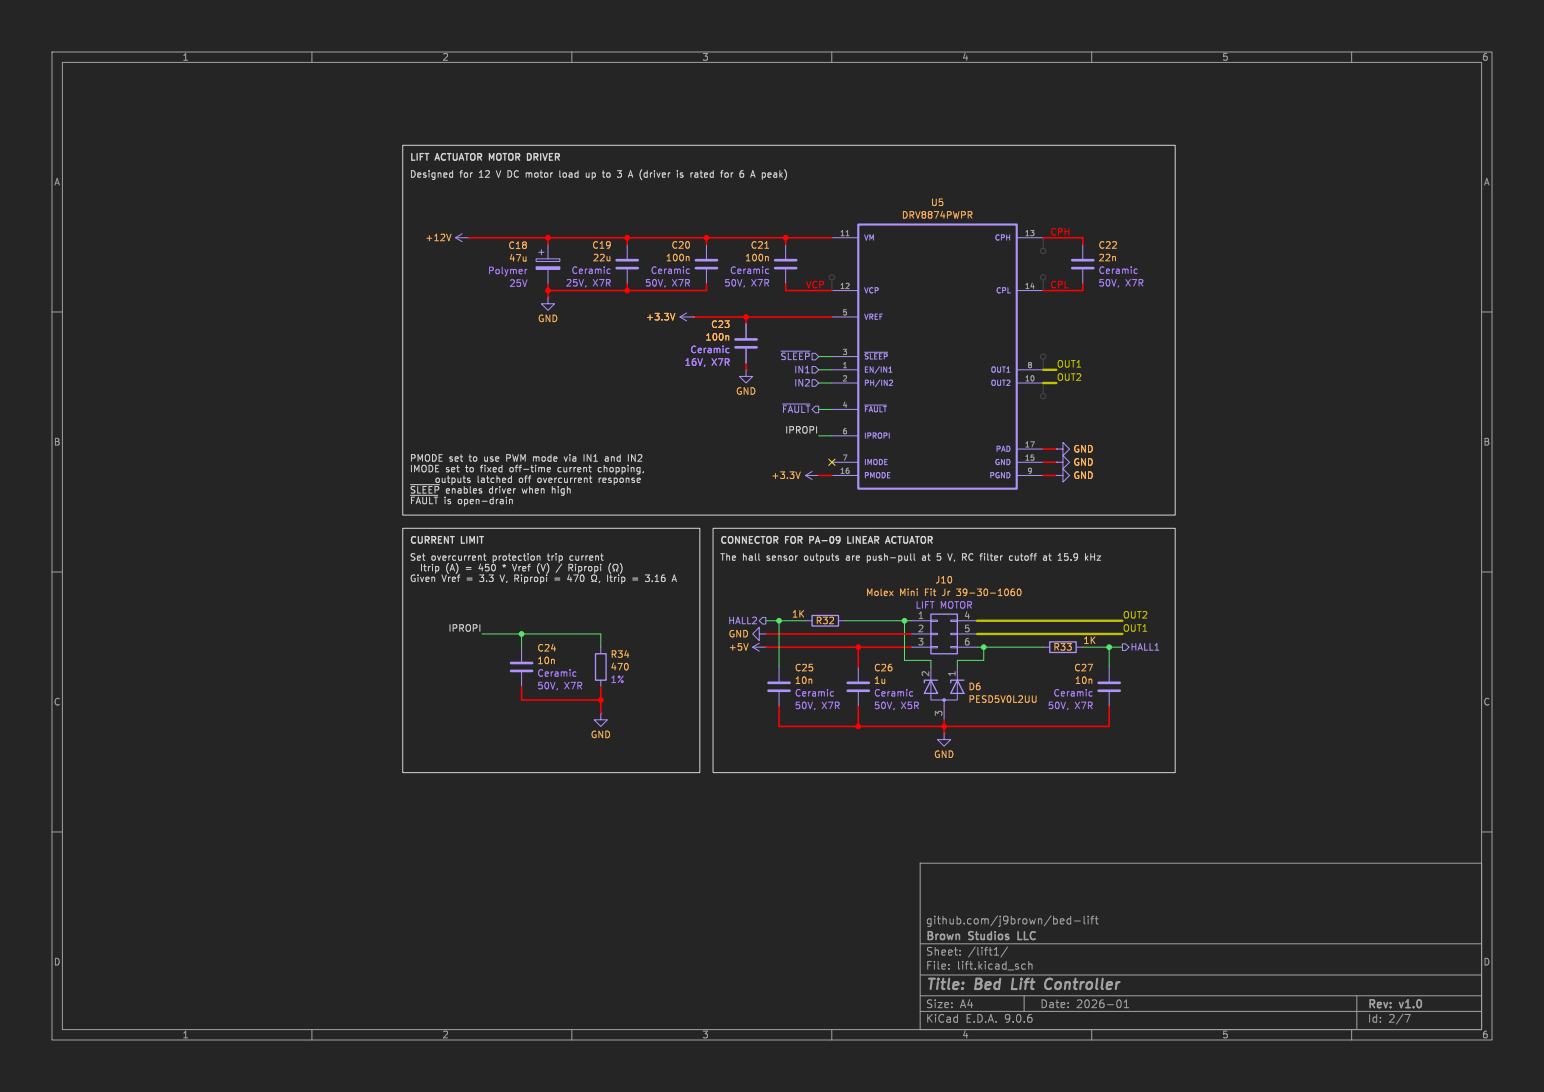
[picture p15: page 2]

Designed for 12 V DC motor load up to 3 A (driver is rated for 6 A peak) LIFT ACTUATOR MOTOR DRIVER

1 D6PESD5V0L2UU GND GND GND GND

CURRENT LIMIT PMODE set to use PWM mode via IN1 and IN2

Itrip (A) = 450 * Vref (V) / Ripropi þÿ(!&) Given Vref = 3.3 V, Ripropi = 470 þÿ!&, Itrip = 3.16 A

J10 Molex Mini Fit Jr 39-30-1060

github.com/j9brown/bed-lift

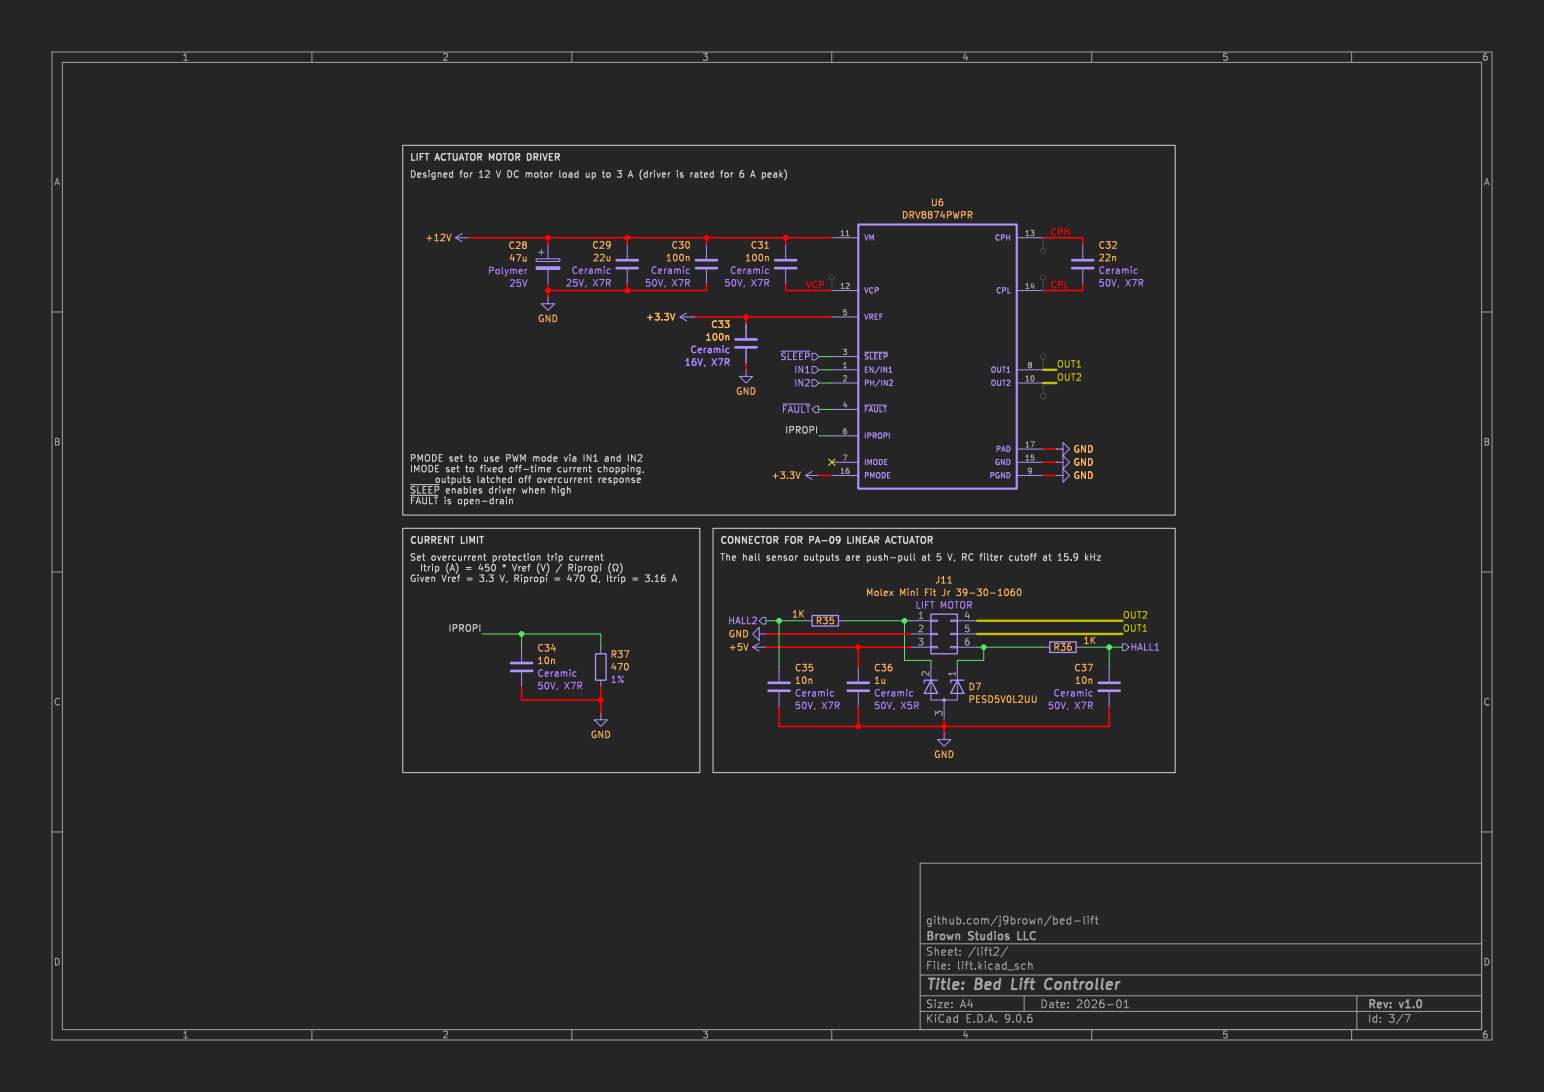
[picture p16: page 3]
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

CURRENT LIMIT PMODE set to use PWM mode via IN1 and IN2

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

J11 Molex Mini Fit Jr 39-30-1060

github.com/j9brown/bed-lift

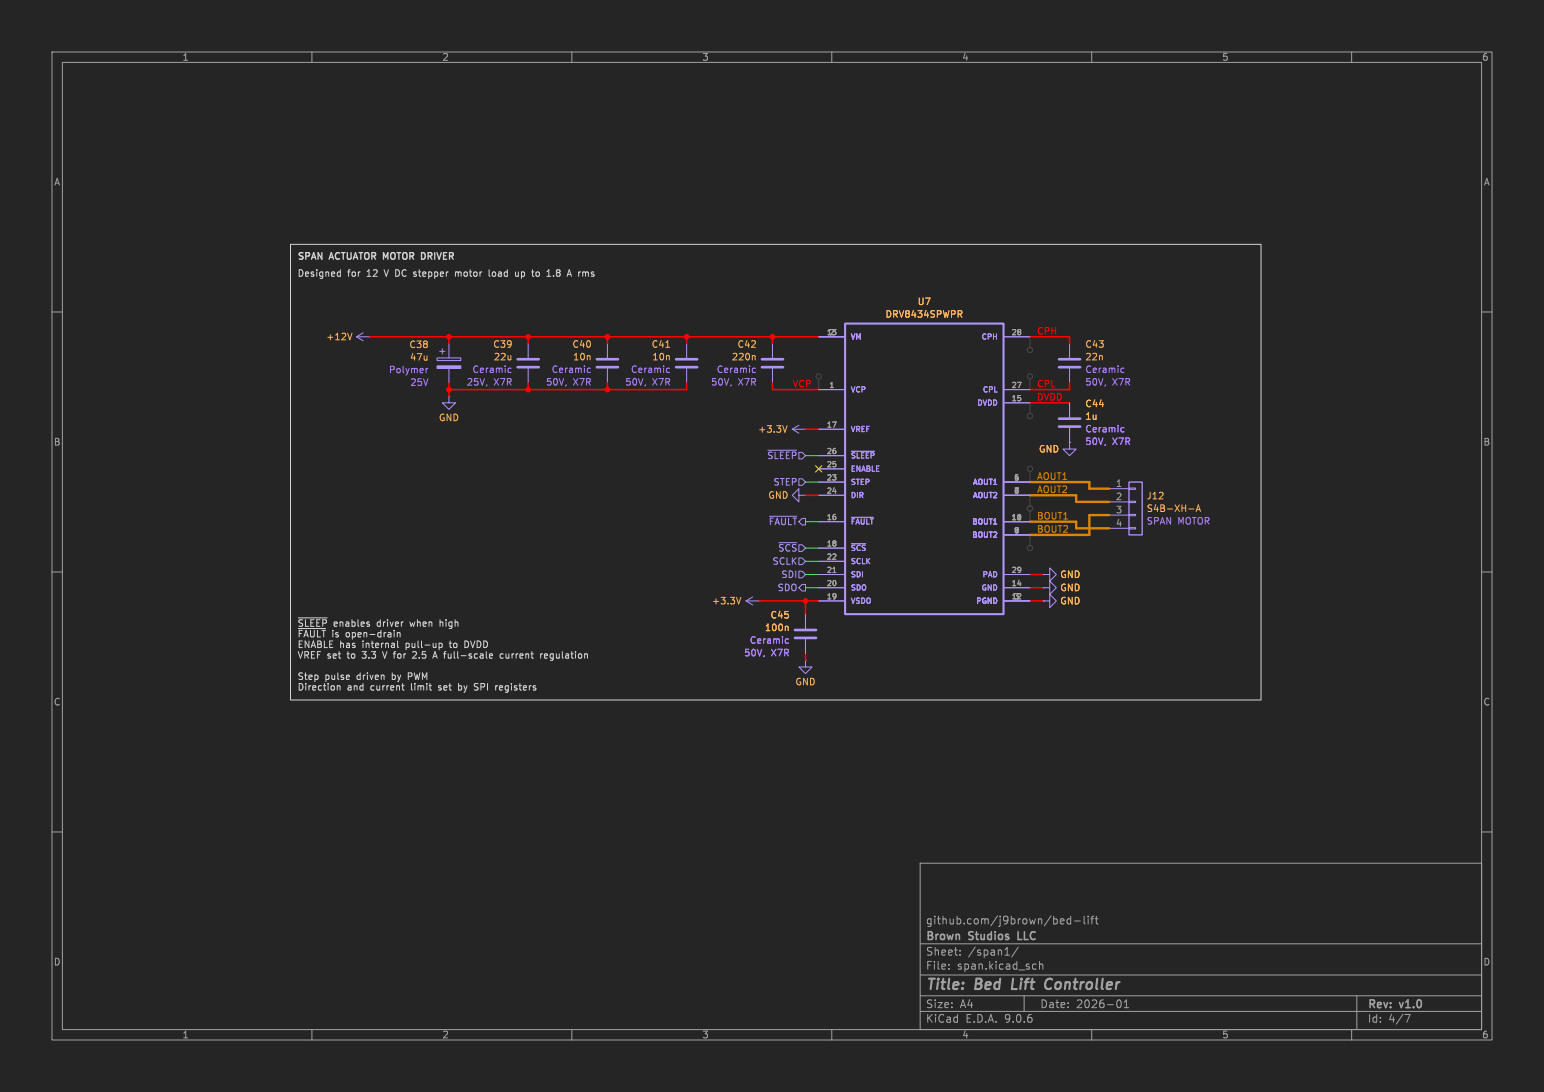
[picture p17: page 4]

SPAN ACTUATOR MOTOR DRIVER

github.com/j9brown/bed-lift GND

Step pulse driven by PWM

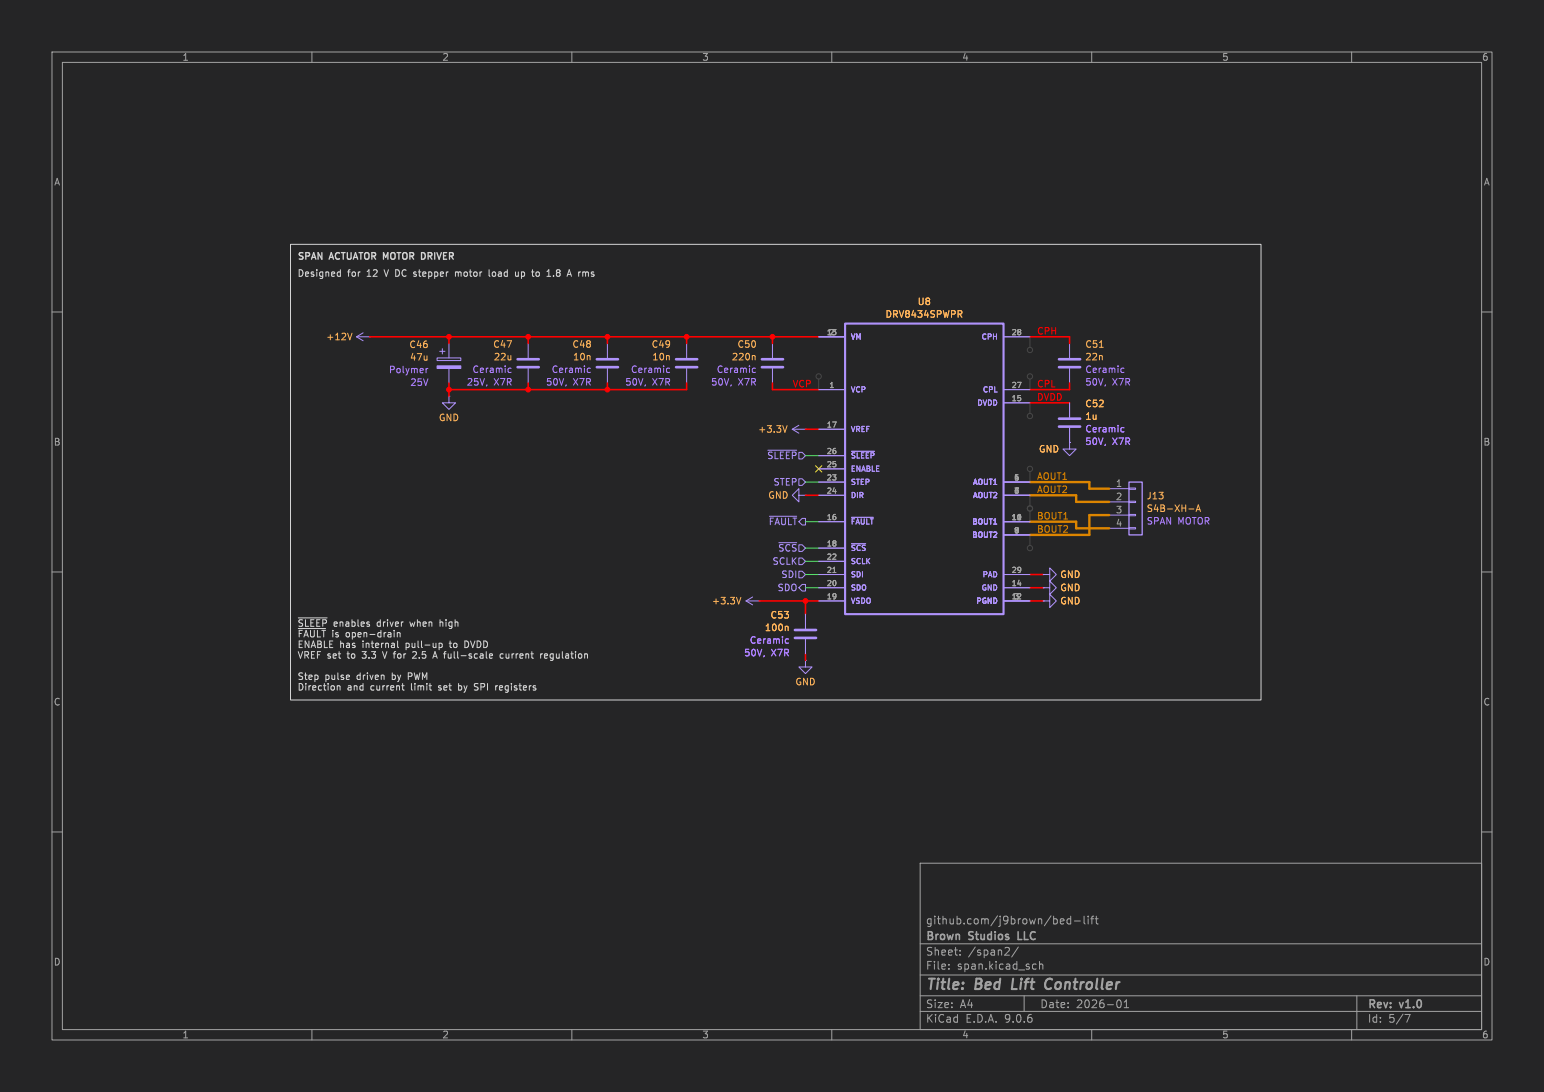
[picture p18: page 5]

BOUT1 CPL SPAN ACTUATOR MOTOR DRIVER
Designed for 12 V DC stepper motor load up to 1.8 A rms ~{SLEEP}enables driver when high

Step pulse driven by PWM

github.com/j9brown/bed-lift

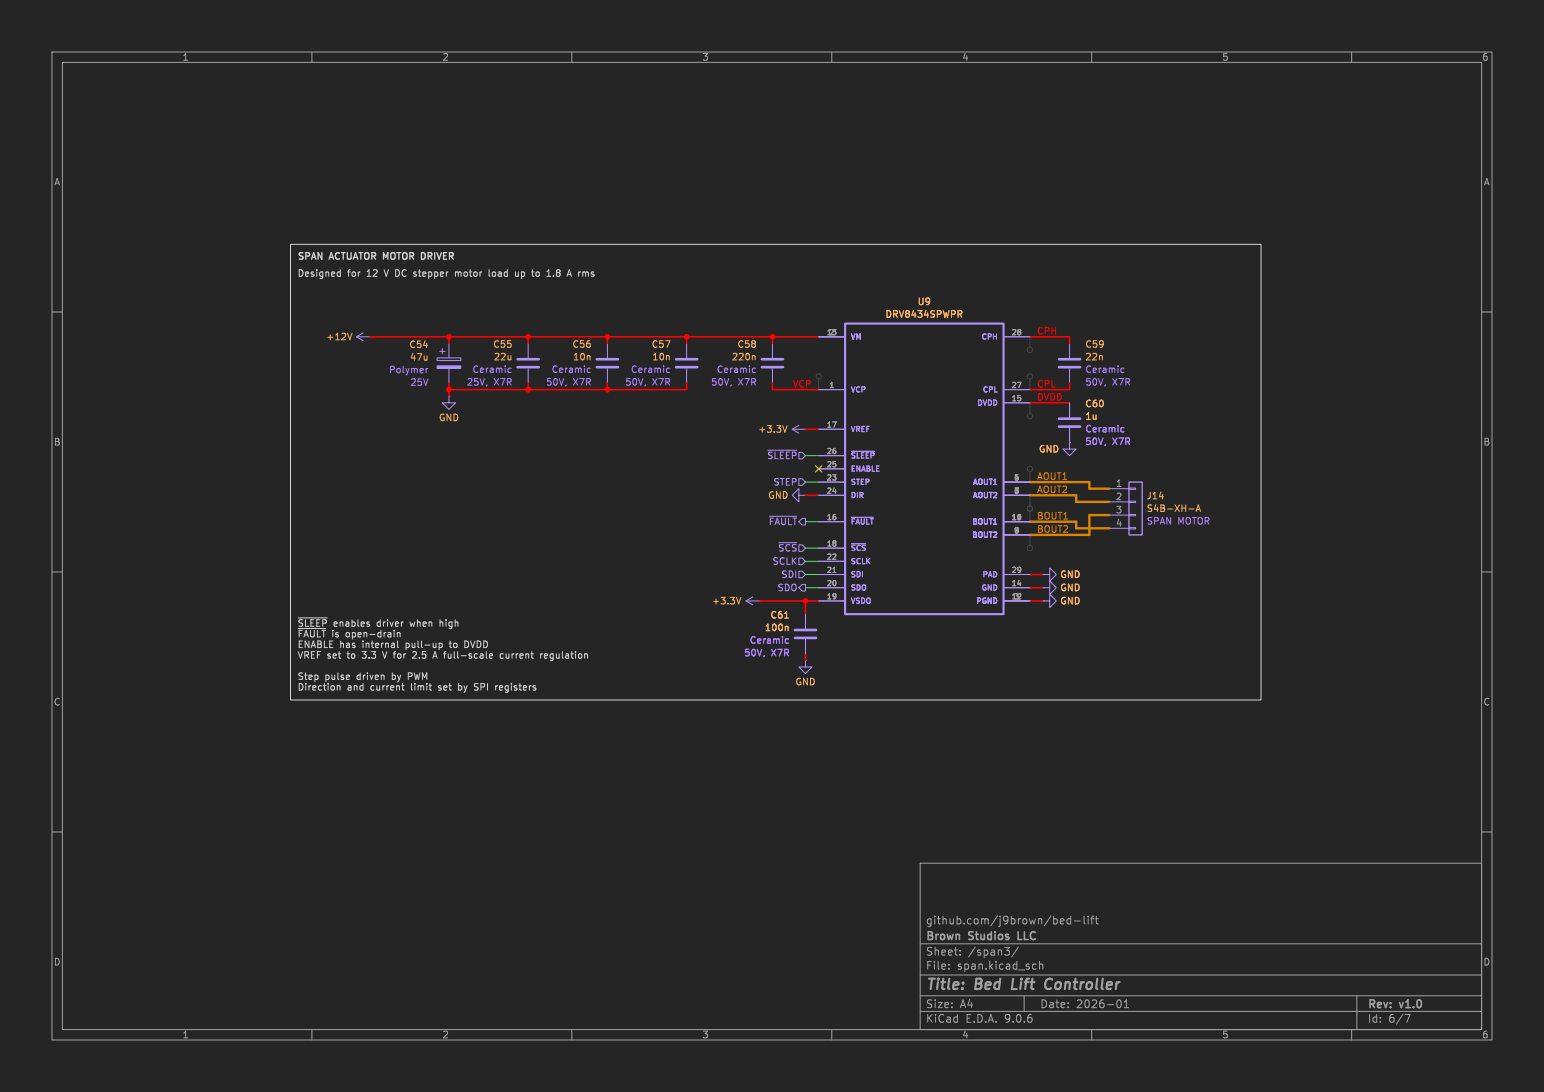
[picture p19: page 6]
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

Step pulse driven by PWM

github.com/j9brown/bed-lift

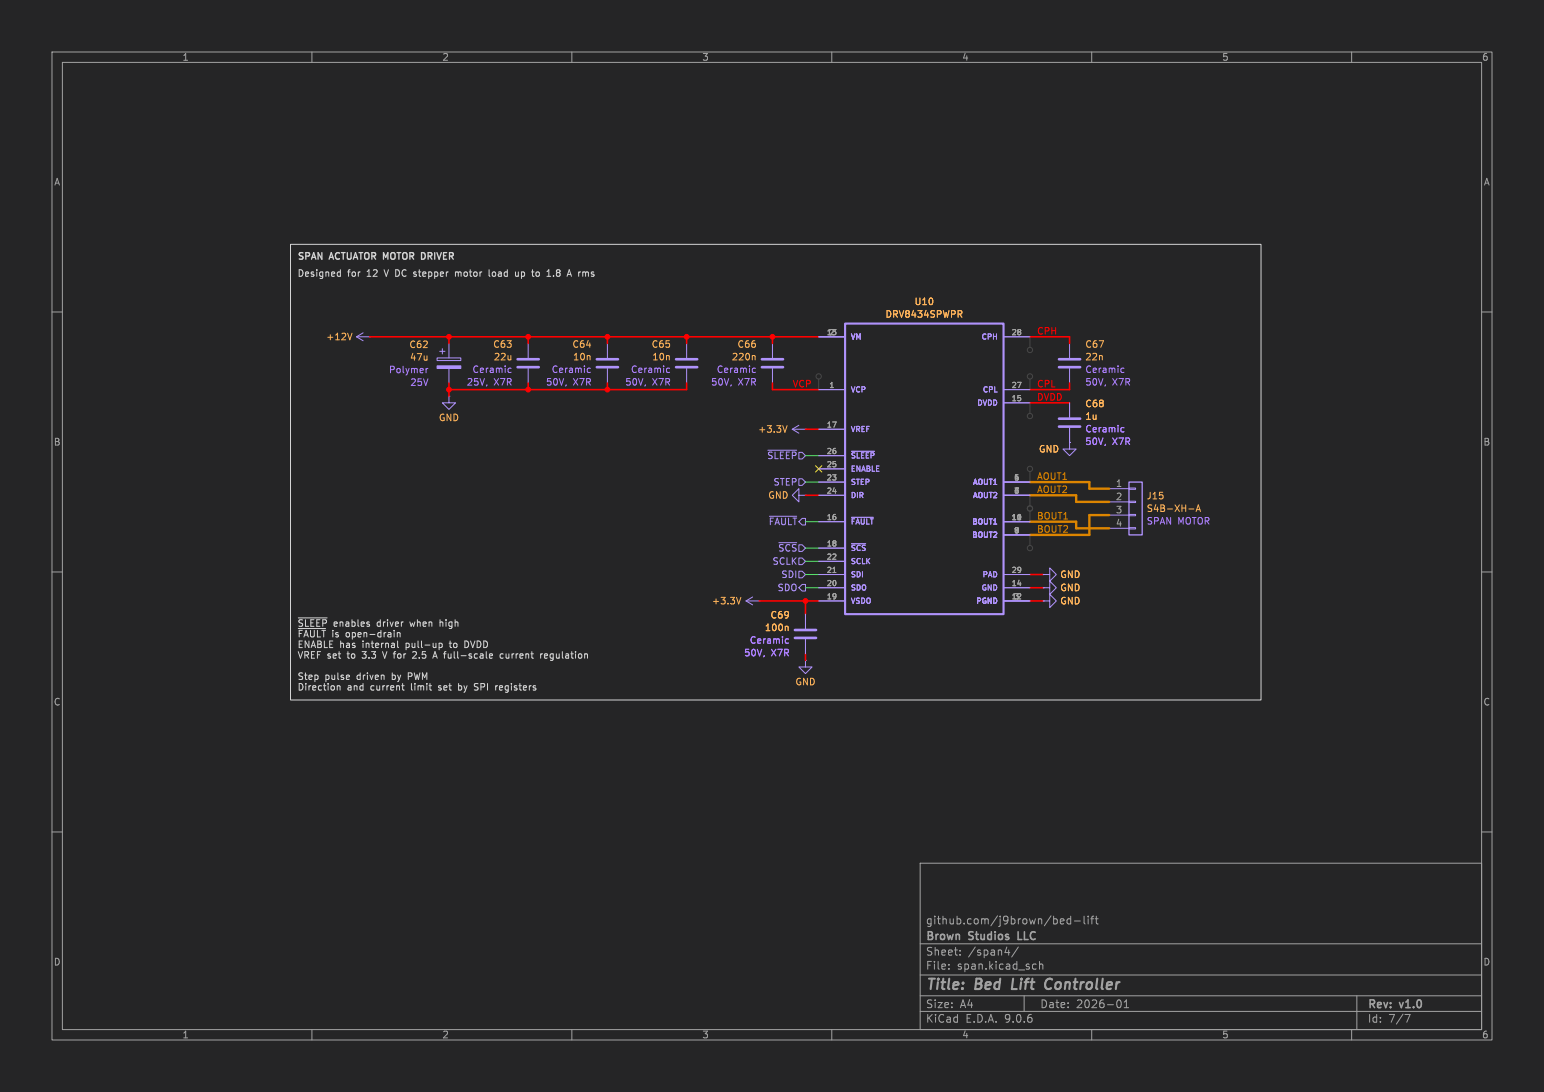
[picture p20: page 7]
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

Step pulse driven by PWM

github.com/j9brown/bed-lift

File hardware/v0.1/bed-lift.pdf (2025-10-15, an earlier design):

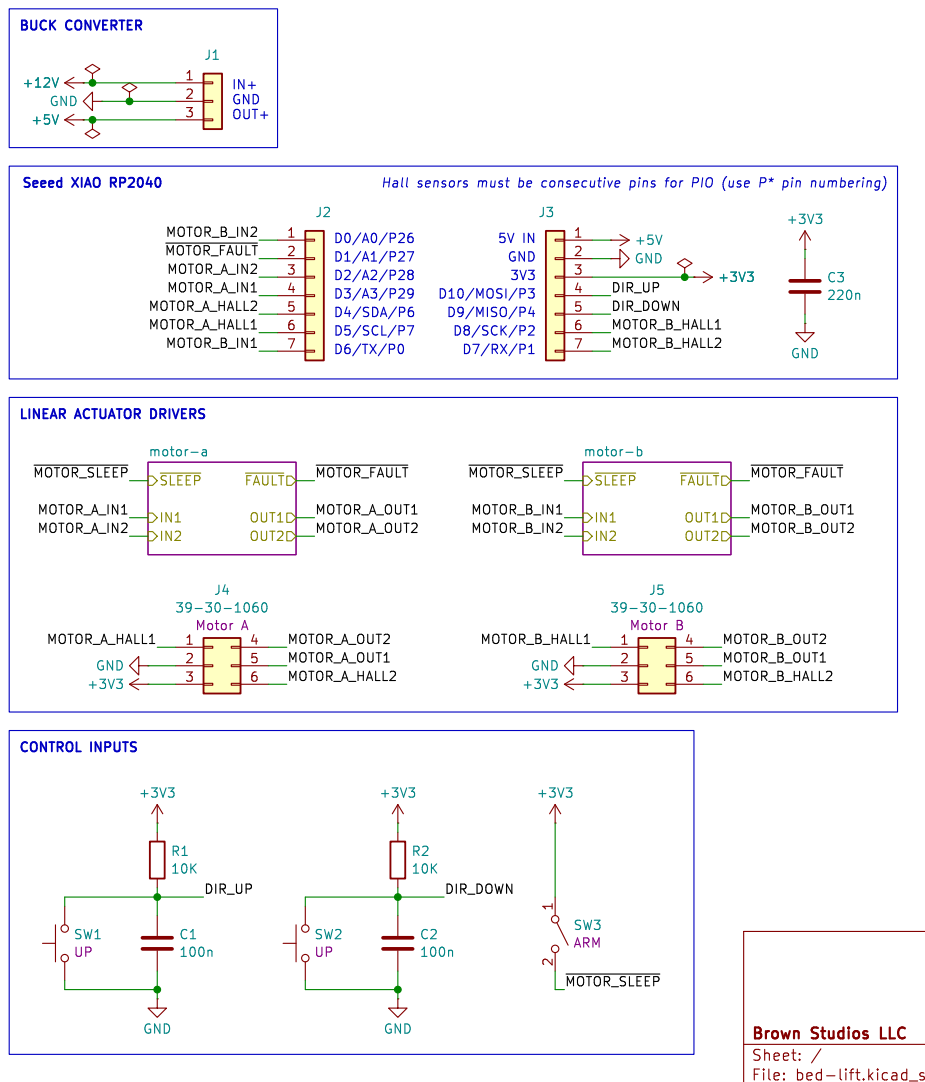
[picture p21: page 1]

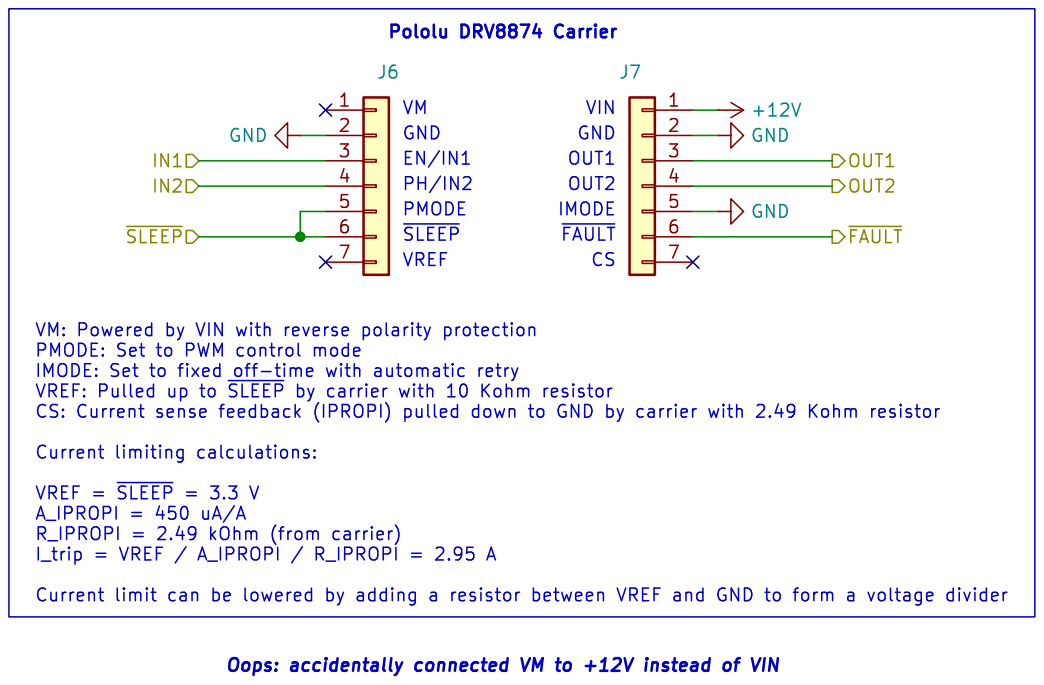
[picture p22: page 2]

VIN GND OUT2 OUT1 Pololu DRV8874 Carrier EN/IN1 VM

A_IPROPI = 450 uA/A R_IPROPI = 2.49 kOhm (from carrier)

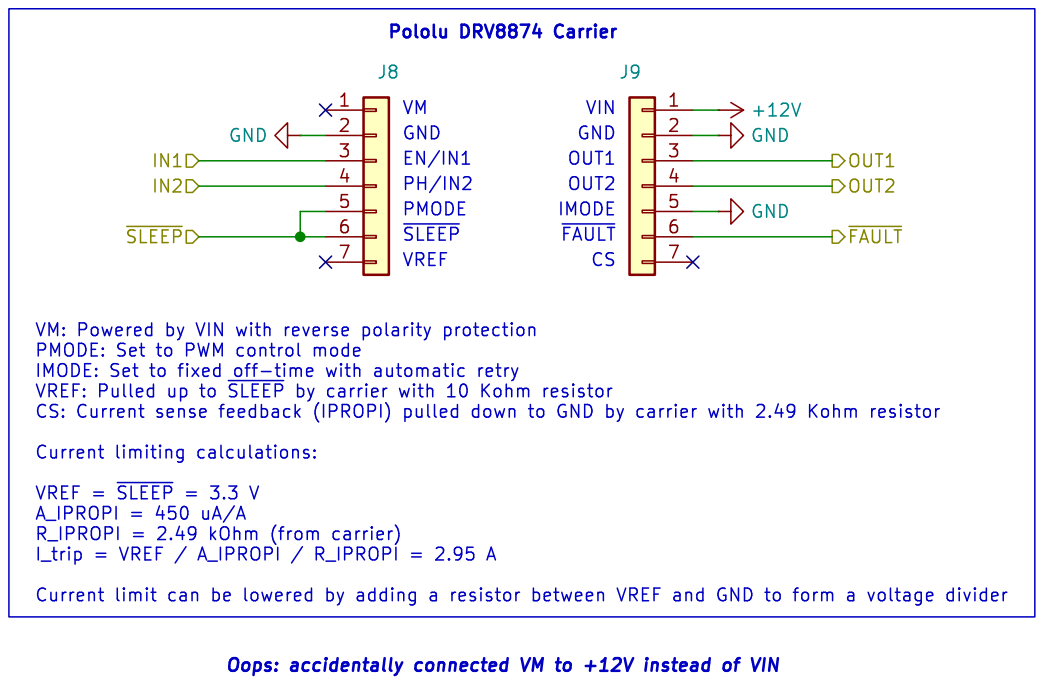
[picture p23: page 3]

VIN GND OUT2 OUT1 Pololu DRV8874 Carrier EN/IN1 VM

A_IPROPI = 450 uA/A R_IPROPI = 2.49 kOhm (from carrier)

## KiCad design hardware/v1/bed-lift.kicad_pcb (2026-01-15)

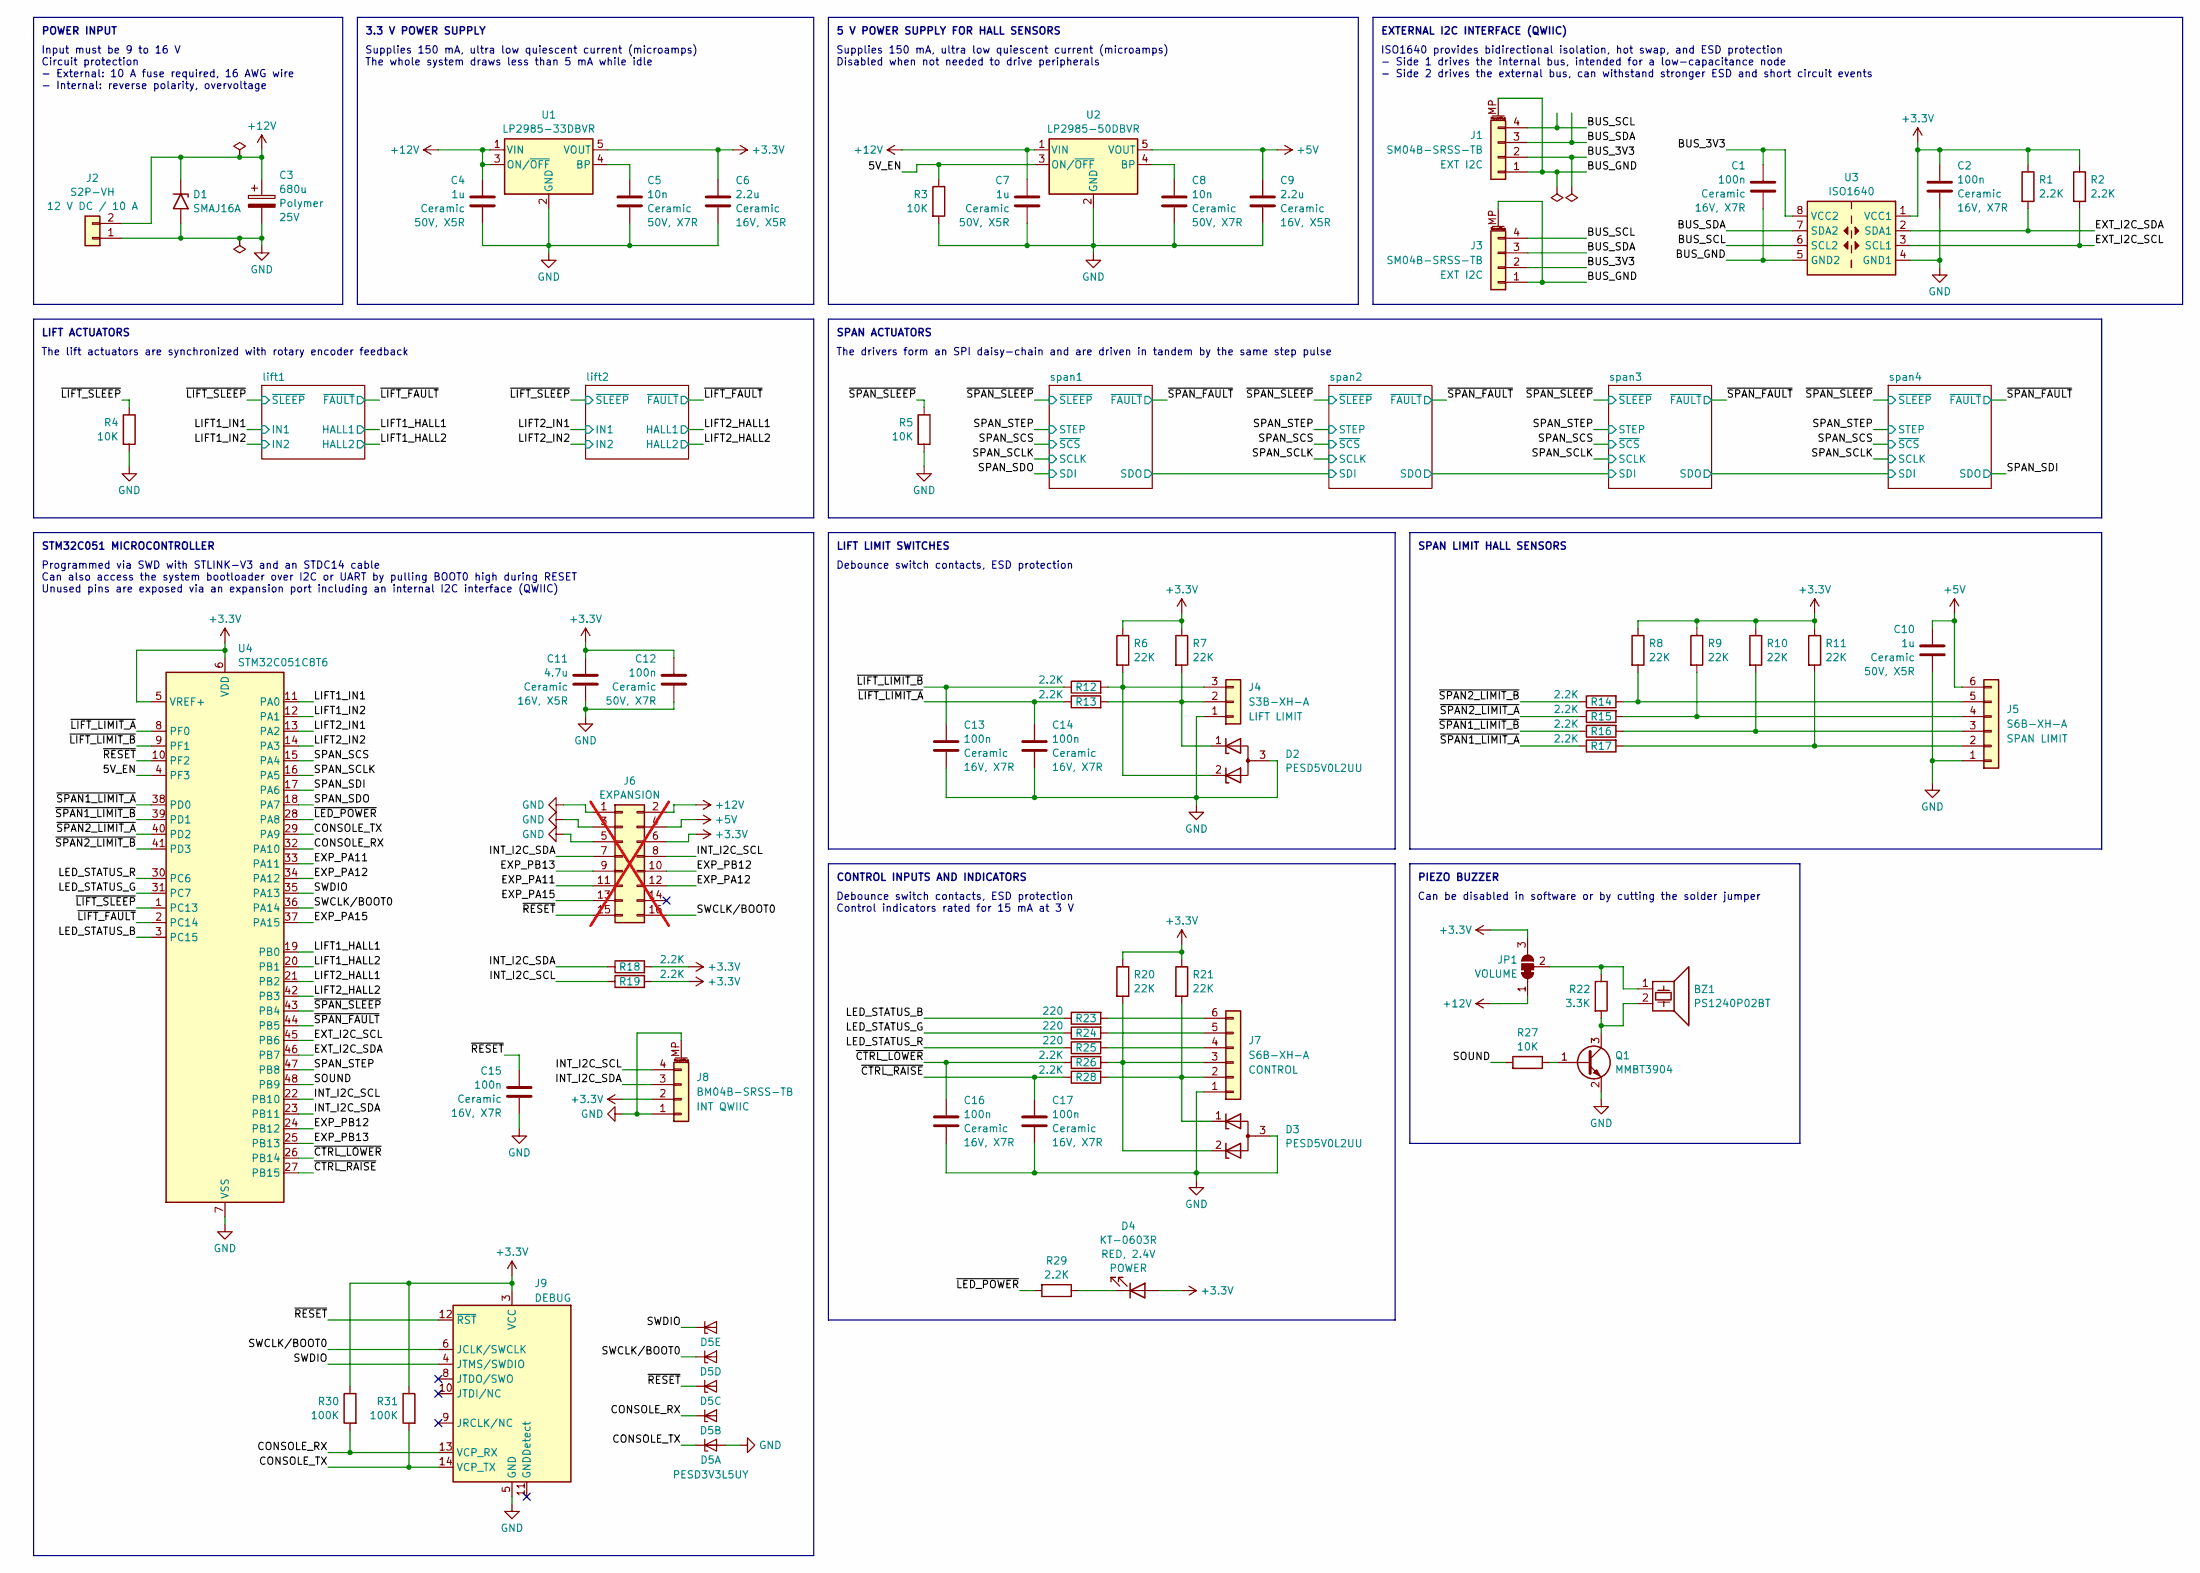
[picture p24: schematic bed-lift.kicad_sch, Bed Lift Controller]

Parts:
BZ1: PS1240P02BT; Buzzer_TDK_PS1240P02BT_D12.2mm_H6.5mm; LCSC C76871
C1, C2, C13, C14, C15, C16, C17: 100n; C_0402_1005Metric; Rating 16V, X7R; LCSC C1525
C3: 680u; CP_Radial_D8.0mm_P3.50mm; Rating 25V; Part Alternative A750KW687M1EAAE016; LCSC C5243855
C4, C7, C10: 1u; C_0603_1608Metric; Rating 50V, X5R; LCSC C15849
C5, C8: 10n; C_0402_1005Metric; Rating 50V, X7R; LCSC C15195
C6, C9: 2.2u; C_0603_1608Metric; Rating 16V, X5R; LCSC C23630
C11: 4.7u; C_0603_1608Metric; Rating 16V, X5R; LCSC C19666
C12: 100n; C_0603_1608Metric; Rating 50V, X7R; LCSC C14663
D1: SMAJ16A; D_SMA; LCSC C74561
D2, D3: PESD5V0L2UU; SOT-323_SC-70; LCSC C78769
D4: KT-0603R; LED_0603_1608Metric; Rating RED, 2.4V; LCSC C2286
D5: PESD3V3L5UY; SOT-363_SC-70-6; LCSC C3021133
J1, J3: SM04B-SRSS-TB; JST_SH_SM04B-SRSS-TB_1x04-1MP_P1.00mm_Horizontal; Part Alternative GT-A1002WRS-104SBT01; LCSC C160404
J2: S2P-VH; JST_VH_S2P-VH_1x02_P3.96mm_Horizontal; LCSC C160355
J4: S3B-XH-A; JST_XH_S3B-XH-A_1x03_P2.50mm_Horizontal; LCSC C157928
J5, J7: S6B-XH-A; JST_XH_S6B-XH-A_1x06_P2.50mm_Horizontal; LCSC C157919
J6: Conn_02x08_Odd_Even; PinSocket_2x08_P2.54mm_Vertical; not fitted
J8: BM04B-SRSS-TB; JST_SH_BM04B-SRSS-TB_1x04-1MP_P1.00mm_Vertical; LCSC C160390
J9: Conn_ST_STDC14; SAMTEC_FTSH-107-01-L-DV-K-A; LCSC C5563894
JP1: SolderJumper_3_Bridged12; SolderJumper-3_P1.3mm_Bridged12_RoundedPad1.0x1.5mm
Q1: MMBT3904; SOT-23; LCSC C20526
R1, R2, R12, R13, R14, R15, R16, R17, R18, R19, R26, R28, R29: 2.2K; R_0402_1005Metric; LCSC C25879
R3, R4, R5, R27: 10K; R_0402_1005Metric; LCSC C25744
R6, R7, R8, R9, R10, R11, R20, R21: 22K; R_0402_1005Metric; LCSC C25768
R22: 3.3K; R_0603_1608Metric; LCSC C22978
R23, R24, R25: 220; R_0402_1005Metric; LCSC C25091
R30, R31: 100K; R_0402_1005Metric; LCSC C25741
U1: LP2985-33DBVR; SOT-23-5; LCSC C95414
U2: LP2985-50DBVR; SOT-23-5; LCSC C74511
U3: ISO1640; SOIC-8_3.9x4.9mm_P1.27mm; LCSC C5122339
U4: STM32C051C8T6; LQFP-48_7x7mm_P0.5mm; LCSC C45870050

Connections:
+3.3V: C2.1, C6.2, C11.1, C12.1, D4.2 (A), J6.6, J8.2, J9.3 (VCC), JP1.3 (B), R1.1, R2.1, R6.1, R7.1, R8.1, R9.1, R10.1, R11.1, R18.2, R19.2, R20.1, R21.1, R30.1, R31.1, U1.5 (VOUT), U3.1 (VCC1), U4.5 (VREF+), U4.6 (VDD); also elsewhere on the board
+5V: C9.2, C10.1, J5.6, J6.4, U2.5 (VOUT); also elsewhere on the board
+12V: C3.1, C4.1, C7.1, D1.1 (A1), J2.2, J6.2, JP1.1 (A), U1.1 (VIN), U1.3 (ON/~OFF), U2.1 (VIN); also elsewhere on the board
/5V_EN: R3.1, U2.3 (ON/~OFF), U4.4 (PF3)
/BUS_3V3: C1.1, J1.2, J3.2, U3.8 (VCC2)
/BUS_GND: C1.2, J1.1, J1.MP (MountPin), J3.1, J3.MP (MountPin), U3.5 (GND2)
/BUS_SCL: J1.4, J3.4, U3.6 (SCL2)
/BUS_SDA: J1.3, J3.3, U3.7 (SDA2)
/CONSOLE_RX: D5.3 (K2), J9.13 (VCP_RX), R30.2, U4.32 (PA10)
/CONSOLE_TX: D5.1 (K1), J9.14 (VCP_TX), R31.2, U4.29 (PA9)
/EXP_PA11: J6.11, U4.33 (PA11)
/EXP_PA12: J6.12, U4.34 (PA12)
/EXP_PA15: J6.13, U4.37 (PA15)
/EXP_PB12: J6.10, U4.24 (PB12)
/EXP_PB13: J6.9, U4.25 (PB13)
/EXT_I2C_SCL: R2.2, U3.3 (SCL1), U4.45 (PB6)
/EXT_I2C_SDA: R1.2, U3.2 (SDA1), U4.46 (PB7)
/INT_I2C_SCL: J6.8, J8.4, R19.1, U4.22 (PB10)
/INT_I2C_SDA: J6.7, J8.3, R18.1, U4.23 (PB11)
/LED_STATUS_B: R23.1, U4.3 (PC15)
/LED_STATUS_G: R24.1, U4.31 (PC7)
/LED_STATUS_R: R25.1, U4.30 (PC6)
/LIFT1_HALL1: U4.19 (PB0); also elsewhere on the board
/LIFT1_HALL2: U4.20 (PB1); also elsewhere on the board
/LIFT1_IN1: U4.11 (PA0); also elsewhere on the board
/LIFT1_IN2: U4.12 (PA1); also elsewhere on the board
/LIFT2_HALL1: U4.21 (PB2); also elsewhere on the board
/LIFT2_HALL2: U4.42 (PB3); also elsewhere on the board
/LIFT2_IN1: U4.13 (PA2); also elsewhere on the board
/LIFT2_IN2: U4.14 (PA3); also elsewhere on the board
/SOUND: R27.2, U4.48 (PB9)
/SPAN_SCLK: U4.16 (PA5); also elsewhere on the board
/SPAN_SCS: U4.15 (PA4); also elsewhere on the board
/SPAN_SDI: U4.17 (PA6); also elsewhere on the board
/SPAN_SDO: U4.18 (PA7); also elsewhere on the board
/SPAN_STEP: U4.47 (PB8); also elsewhere on the board
/SWCLK/BOOT0: D5.5 (K4), J6.16, J9.6 (JCLK/SWCLK), U4.36 (PA14)
/SWDIO: D5.6 (K5), J9.4 (JTMS/SWDIO), U4.35 (PA13)
/~CTRL_LOWER: C16.1, R26.1, U4.26 (PB14)
/~CTRL_RAISE: C17.1, R28.1, U4.27 (PB15)
/~LED_POWER: R29.2, U4.28 (PA8)
/~LIFT_FAULT: U4.2 (PC14); also elsewhere on the board
/~LIFT_LIMIT_A: C14.1, R13.1, U4.8 (PF0)
/~LIFT_LIMIT_B: C13.1, R12.1, U4.9 (PF1)
/~LIFT_SLEEP: R4.1, U4.1 (PC13); also elsewhere on the board
/~RESET: C15.1, D5.4 (K3), J6.15, J9.12 (~RST), U4.10 (PF2)
/~SPAN1_LIMIT_A: R17.1, U4.38 (PD0)
/~SPAN1_LIMIT_B: R16.1, U4.39 (PD1)
/~SPAN2_LIMIT_A: R15.1, U4.40 (PD2)
/~SPAN2_LIMIT_B: R14.1, U4.41 (PD3)
/~SPAN_FAULT: U4.44 (PB5); also elsewhere on the board
/~SPAN_SLEEP: R5.1, U4.43 (PB4); also elsewhere on the board
GND: C2.2, C3.2, C4.2, C5.1, C6.1, C7.2, C8.1, C9.1, C10.2, C11.2, C12.2, C13.2, C14.2, C15.2, C16.2, C17.2, D1.2 (A2), D2.3 (A), D3.3 (A), D5.2 (A), J2.1, J4.1, J5.1, J6.1, J6.3, J6.5, J7.1, J8.1, J8.MP (MountPin), J9.5 (GND), J9.7 (GND), Q1.2 (E), R3.2, R4.2, R5.2, U1.2 (GND), U2.2 (GND), U3.4 (GND1), U4.7 (VSS); also elsewhere on the board
unnamed: D4.1 (K), R29.1
unnamed: D2.1 (K), J4.2, R7.2, R13.2
unnamed: D2.2 (K), J4.3, R6.2, R12.2
unnamed: J5.2, R11.2, R17.2
unnamed: J5.3, R10.2, R16.2
unnamed: J5.4, R9.2, R15.2
unnamed: J5.5, R8.2, R14.2
unnamed: D3.1 (K), J7.2, R21.2, R28.2
unnamed: D3.2 (K), J7.3, R20.2, R26.2
unnamed: J7.4, R25.2
unnamed: J7.5, R24.2
unnamed: J7.6, R23.2
unnamed: BZ1.1, JP1.2 (C), R22.1
unnamed: Q1.1 (B), R27.1
unnamed: BZ1.2, Q1.3 (C), R22.2
unnamed: C5.2, U1.4 (BP)
unnamed: C8.2, U2.4 (BP)

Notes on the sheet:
Programmed via SWD with STLINK-V3 and an STDC14 cable Can also access the system bootloader over I2C or UART by pulling BOOT0 high during RESET Unused pins are exposed via an expansion port including an internal I2C interface (QWIIC)
Supplies 150 mA, ultra low quiescent current (microamps) The whole system draws less than 5 mA while idle
LIFT LIMIT SWITCHES
POWER INPUT
5 V POWER SUPPLY FOR HALL SENSORS
The lift actuators are synchronized with rotary encoder feedback
SPAN ACTUATORS
Can be disabled in software or by cutting the solder jumper
STM32C051 MICROCONTROLLER
3.3 V POWER SUPPLY
Supplies 150 mA, ultra low quiescent current (microamps) Disabled when not needed to drive peripherals
EXTERNAL I2C INTERFACE (QWIIC)
SPAN LIMIT HALL SENSORS
PIEZO BUZZER
The drivers form an SPI daisy-chain and are driven in tandem by the same step pulse
CONTROL INPUTS AND INDICATORS
Input must be 9 to 16 V Circuit protection - External: 10 A fuse required, 16 AWG wire - Internal: reverse polarity, overvoltage
ISO1640 provides bidirectional isolation, hot swap, and ESD protection - Side 1 drives the internal bus, intended for a low-capacitance node - Side 2 drives the external bus, can withstand stronger ESD and short circuit events
LIFT ACTUATORS
Debounce switch contacts, ESD protection Control indicators rated for 15 mA at 3 V
Debounce switch contacts, ESD protection

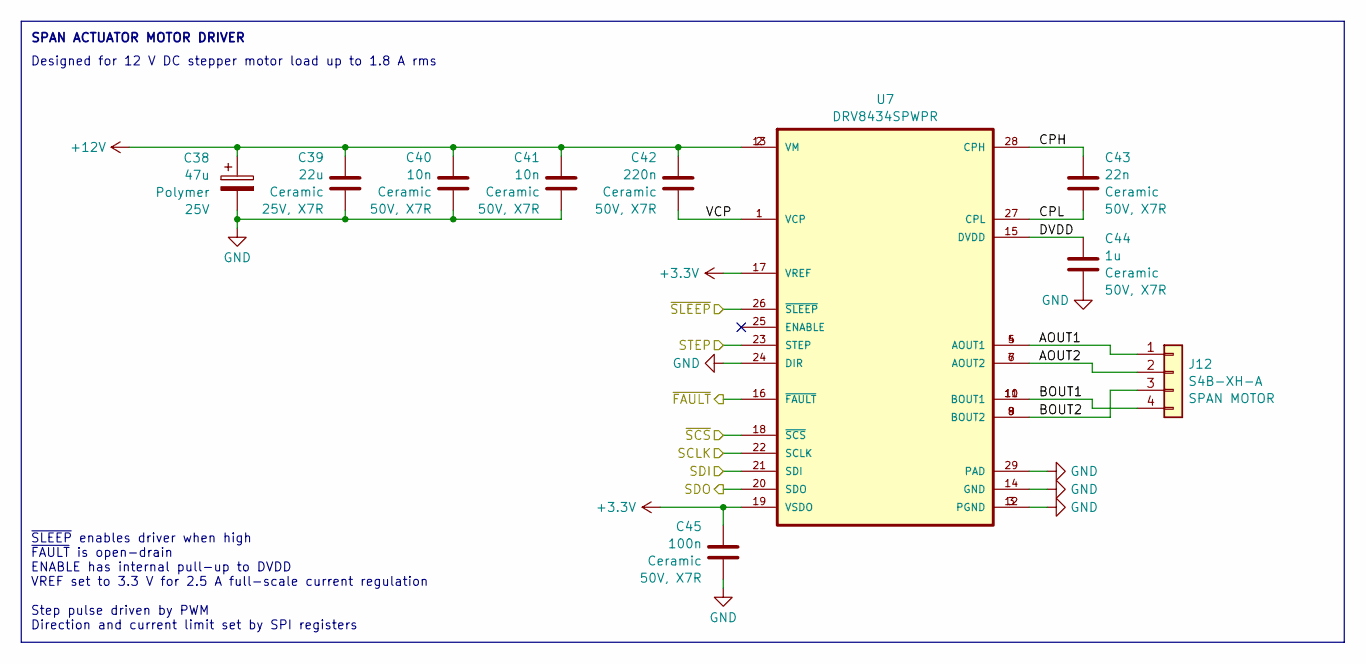
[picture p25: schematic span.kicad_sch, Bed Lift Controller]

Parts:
C38: 47u; CP_Radial_D5.0mm_P2.50mm; Rating 25V; Part 4700250508R00; LCSC C5243872
C39: 22u; C_1210_3225Metric; Rating 25V, X7R; LCSC C309062
C40, C41: 10n; C_0603_1608Metric; Rating 50V, X7R; LCSC C57112
C42: 220n; C_0603_1608Metric; Rating 50V, X7R; LCSC C21120
C43: 22n; C_0603_1608Metric; Rating 50V, X7R; LCSC C21122
C44: 1u; C_0805_2012Metric; Rating 50V, X7R; LCSC C28323
C45: 100n; C_0603_1608Metric; Rating 50V, X7R; LCSC C14663
J12: S4B-XH-A; JST_XH_S4B-XH-A_1x04_P2.50mm_Horizontal; LCSC C157925
U7: DRV8434SPWPR; HTSSOP-28 PWP0028M; LCSC C3681202

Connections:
+3.3V: C45.1, U7.17 (VREF), U7.19 (VSDO); also elsewhere on the board
+12V: C38.1, C39.2, C40.1, C41.1, C42.1, U7.2 (VM), U7.13 (VM); also elsewhere on the board
/SPAN_SCLK: U7.22 (SCLK); also elsewhere on the board
/SPAN_SCS: U7.18 (~SCS); also elsewhere on the board
/SPAN_SDO: U7.21 (SDI); also elsewhere on the board
/SPAN_STEP: U7.23 (STEP); also elsewhere on the board
/span1/AOUT1: J12.1, U7.4 (AOUT1), U7.5 (AOUT1)
/span1/AOUT2: J12.2, U7.6 (AOUT2), U7.7 (AOUT2)
/span1/BOUT1: J12.4, U7.10 (BOUT1), U7.11 (BOUT1)
/span1/BOUT2: J12.3, U7.8 (BOUT2), U7.9 (BOUT2)
/span1/CPH: C43.1, U7.28 (CPH)
/span1/CPL: C43.2, U7.27 (CPL)
/span1/DVDD: C44.1, U7.15 (DVDD)
/span1/SDO: U7.20 (SDO); also elsewhere on the board
/span1/VCP: C42.2, U7.1 (VCP)
/~SPAN_FAULT: U7.16 (~FAULT); also elsewhere on the board
/~SPAN_SLEEP: U7.26 (~SLEEP); also elsewhere on the board
GND: C38.2, C39.1, C40.2, C41.2, C44.2, C45.2, U7.3 (PGND), U7.12 (PGND), U7.14 (GND), U7.24 (DIR), U7.29 (PAD); also elsewhere on the board

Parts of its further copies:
C46, C54, C62: 47u; CP_Radial_D5.0mm_P2.50mm; Rating 25V; Part 4700250508R00; LCSC C5243872
C47, C55, C63: 22u; C_1210_3225Metric; Rating 25V, X7R; LCSC C309062
C48, C49, C56, C57, C64, C65: 10n; C_0603_1608Metric; Rating 50V, X7R; LCSC C57112
C50, C58, C66: 220n; C_0603_1608Metric; Rating 50V, X7R; LCSC C21120
C51, C59, C67: 22n; C_0603_1608Metric; Rating 50V, X7R; LCSC C21122
C52, C60, C68: 1u; C_0805_2012Metric; Rating 50V, X7R; LCSC C28323
C53, C61, C69: 100n; C_0603_1608Metric; Rating 50V, X7R; LCSC C14663
J13, J14, J15: S4B-XH-A; JST_XH_S4B-XH-A_1x04_P2.50mm_Horizontal; LCSC C157925
U8, U9, U10: DRV8434SPWPR; HTSSOP-28 PWP0028M; LCSC C3681202

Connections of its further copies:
+3.3V: C53.1, C61.1, C69.1, U8.17 (VREF), U8.19 (VSDO), U9.17 (VREF), U9.19 (VSDO), U10.17 (VREF), U10.19 (VSDO); also elsewhere on the board
+12V: C46.1, C47.2, C48.1, C49.1, C50.1, C54.1, C55.2, C56.1, C57.1, C58.1, C62.1, C63.2, C64.1, C65.1, C66.1, U8.2 (VM), U8.13 (VM), U9.2 (VM), U9.13 (VM), U10.2 (VM), U10.13 (VM); also elsewhere on the board
/SPAN_SCLK: U8.22 (SCLK), U9.22 (SCLK), U10.22 (SCLK); also elsewhere on the board
/SPAN_SCS: U8.18 (~SCS), U9.18 (~SCS), U10.18 (~SCS); also elsewhere on the board
/SPAN_SDI: U10.20 (SDO); also elsewhere on the board
/SPAN_STEP: U8.23 (STEP), U9.23 (STEP), U10.23 (STEP); also elsewhere on the board
/span1/SDO: U8.21 (SDI); also elsewhere on the board
/span2/AOUT1: J13.1, U8.4 (AOUT1), U8.5 (AOUT1)
/span2/AOUT2: J13.2, U8.6 (AOUT2), U8.7 (AOUT2)
/span2/BOUT1: J13.4, U8.10 (BOUT1), U8.11 (BOUT1)
/span2/BOUT2: J13.3, U8.8 (BOUT2), U8.9 (BOUT2)
/span2/CPH: C51.1, U8.28 (CPH)
/span2/CPL: C51.2, U8.27 (CPL)
/span2/DVDD: C52.1, U8.15 (DVDD)
/span2/SDO: U8.20 (SDO), U9.21 (SDI)
/span2/VCP: C50.2, U8.1 (VCP)
/span3/AOUT1: J14.1, U9.4 (AOUT1), U9.5 (AOUT1)
/span3/AOUT2: J14.2, U9.6 (AOUT2), U9.7 (AOUT2)
/span3/BOUT1: J14.4, U9.10 (BOUT1), U9.11 (BOUT1)
/span3/BOUT2: J14.3, U9.8 (BOUT2), U9.9 (BOUT2)
/span3/CPH: C59.1, U9.28 (CPH)
/span3/CPL: C59.2, U9.27 (CPL)
/span3/DVDD: C60.1, U9.15 (DVDD)
/span3/SDO: U9.20 (SDO), U10.21 (SDI)
/span3/VCP: C58.2, U9.1 (VCP)
/span4/AOUT1: J15.1, U10.4 (AOUT1), U10.5 (AOUT1)
/span4/AOUT2: J15.2, U10.6 (AOUT2), U10.7 (AOUT2)
/span4/BOUT1: J15.4, U10.10 (BOUT1), U10.11 (BOUT1)
/span4/BOUT2: J15.3, U10.8 (BOUT2), U10.9 (BOUT2)
/span4/CPH: C67.1, U10.28 (CPH)
/span4/CPL: C67.2, U10.27 (CPL)
/span4/DVDD: C68.1, U10.15 (DVDD)
/span4/VCP: C66.2, U10.1 (VCP)
/~SPAN_FAULT: U8.16 (~FAULT), U9.16 (~FAULT), U10.16 (~FAULT); also elsewhere on the board
/~SPAN_SLEEP: U8.26 (~SLEEP), U9.26 (~SLEEP), U10.26 (~SLEEP); also elsewhere on the board
GND: C46.2, C47.1, C48.2, C49.2, C52.2, C53.2, C54.2, C55.1, C56.2, C57.2, C60.2, C61.2, C62.2, C63.1, C64.2, C65.2, C68.2, C69.2, U8.3 (PGND), U8.12 (PGND), U8.14 (GND), U8.24 (DIR), U8.29 (PAD), U9.3 (PGND), U9.12 (PGND), U9.14 (GND), U9.24 (DIR), U9.29 (PAD), U10.3 (PGND), U10.12 (PGND), U10.14 (GND), U10.24 (DIR), U10.29 (PAD); also elsewhere on the board

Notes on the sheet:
Designed for 12 V DC stepper motor load up to 1.8 A rms
SPAN ACTUATOR MOTOR DRIVER
~{SLEEP} enables driver when high ~{FAULT} is open-drain ENABLE has internal pull-up to DVDD VREF set to 3.3 V for 2.5 A full-scale current regulation Step pulse driven by PWM Direction and current limit set by SPI registers

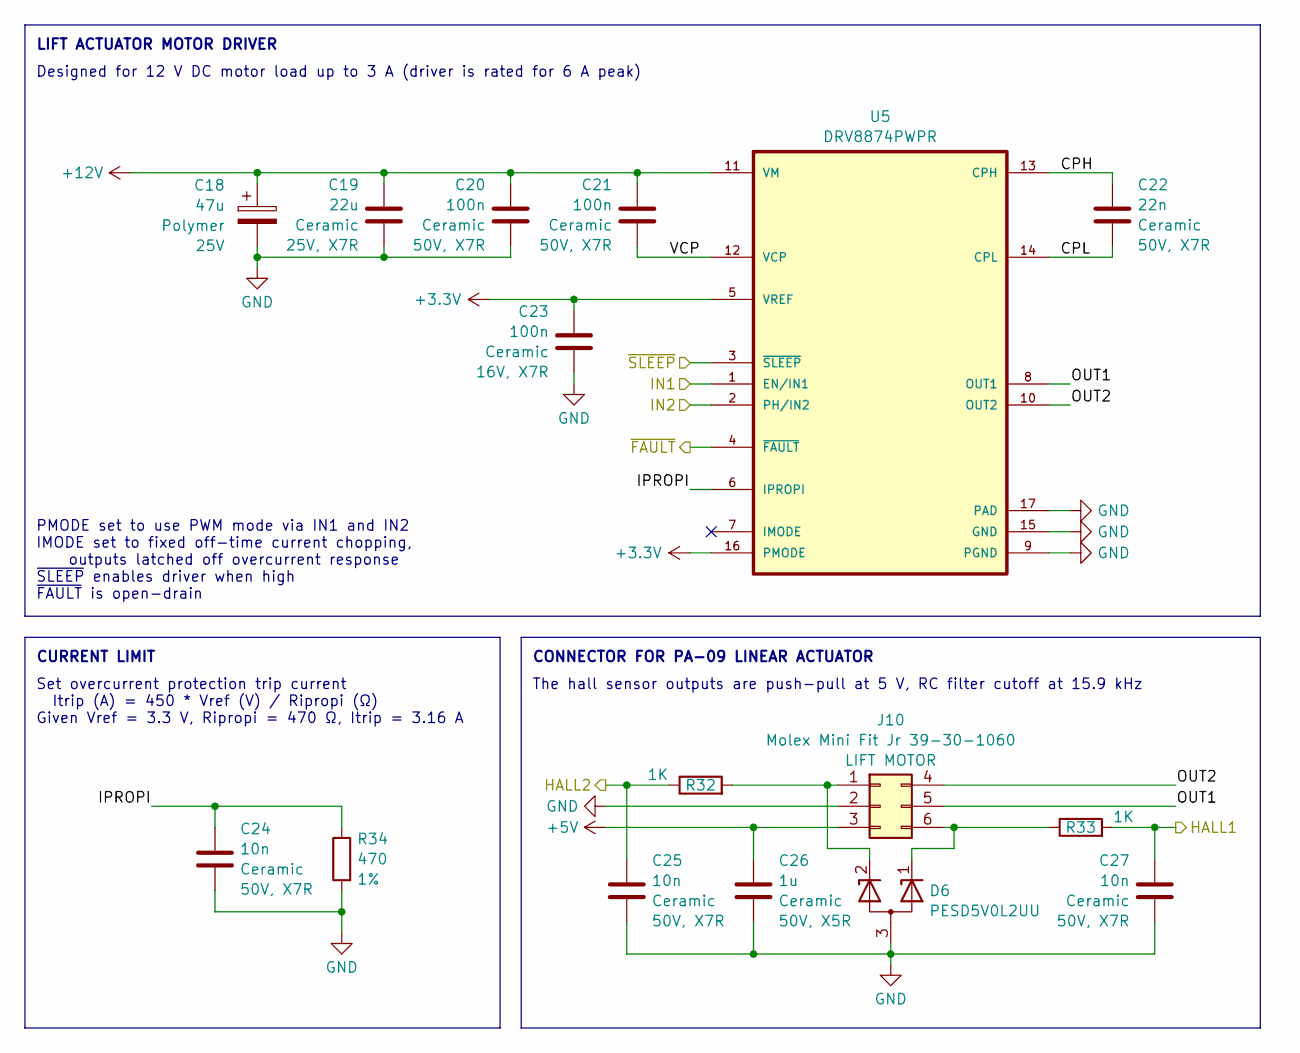
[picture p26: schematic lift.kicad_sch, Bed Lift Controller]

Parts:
C18: 47u; CP_Radial_D5.0mm_P2.50mm; Rating 25V; Part 4700250508R00; LCSC C5243872
C19: 22u; C_1210_3225Metric; Rating 25V, X7R; LCSC C309062
C20, C21: 100n; C_0603_1608Metric; Rating 50V, X7R; LCSC C14663
C22: 22n; C_0603_1608Metric; Rating 50V, X7R; LCSC C21122
C23: 100n; C_0402_1005Metric; Rating 16V, X7R; LCSC C1525
C24, C25, C27: 10n; C_0402_1005Metric; Rating 50V, X7R; LCSC C15195
C26: 1u; C_0603_1608Metric; Rating 50V, X5R; LCSC C15849
D6: PESD5V0L2UU; SOT-323_SC-70; LCSC C78769
J10: Molex Mini Fit Jr 39-30-1060; MOLEX_39301060; LCSC C114098
R32, R33: 1K; R_0402_1005Metric; LCSC C11702
R34: 470; R_0402_1005Metric; Rating 1%; LCSC C25117
U5: DRV8874PWPR; HTSSOP-16 PWP0016J; LCSC C1855818

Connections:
+3.3V: C23.1, U5.5 (VREF), U5.16 (PMODE); also elsewhere on the board
+5V: C26.1, J10.3; also elsewhere on the board
+12V: C18.1, C19.2, C20.1, C21.1, U5.11 (VM); also elsewhere on the board
/LIFT1_HALL1: C27.1, R33.2; also elsewhere on the board
/LIFT1_HALL2: C25.1, R32.1; also elsewhere on the board
/LIFT1_IN1: U5.1 (EN/IN1); also elsewhere on the board
/LIFT1_IN2: U5.2 (PH/IN2); also elsewhere on the board
/lift1/CPH: C22.1, U5.13 (CPH)
/lift1/CPL: C22.2, U5.14 (CPL)
/lift1/IPROPI: C24.1, R34.1, U5.6 (IPROPI)
/lift1/OUT1: J10.5, U5.8 (OUT1)
/lift1/OUT2: J10.4, U5.10 (OUT2)
/lift1/VCP: C21.2, U5.12 (VCP)
/~LIFT_FAULT: U5.4 (~FAULT); also elsewhere on the board
/~LIFT_SLEEP: U5.3 (~SLEEP); also elsewhere on the board
GND: C18.2, C19.1, C20.2, C23.2, C24.2, C25.2, C26.2, C27.2, D6.3 (A), J10.2, R34.2, U5.9 (PGND), U5.15 (GND), U5.17 (PAD); also elsewhere on the board
unnamed: D6.2 (K), J10.1, R32.2
unnamed: D6.1 (K), J10.6, R33.1

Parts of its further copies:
C28: 47u; CP_Radial_D5.0mm_P2.50mm; Rating 25V; Part 4700250508R00; LCSC C5243872
C29: 22u; C_1210_3225Metric; Rating 25V, X7R; LCSC C309062
C30, C31: 100n; C_0603_1608Metric; Rating 50V, X7R; LCSC C14663
C32: 22n; C_0603_1608Metric; Rating 50V, X7R; LCSC C21122
C33: 100n; C_0402_1005Metric; Rating 16V, X7R; LCSC C1525
C34, C35, C37: 10n; C_0402_1005Metric; Rating 50V, X7R; LCSC C15195
C36: 1u; C_0603_1608Metric; Rating 50V, X5R; LCSC C15849
D7: PESD5V0L2UU; SOT-323_SC-70; LCSC C78769
J11: Molex Mini Fit Jr 39-30-1060; MOLEX_39301060; LCSC C114098
R35, R36: 1K; R_0402_1005Metric; LCSC C11702
R37: 470; R_0402_1005Metric; Rating 1%; LCSC C25117
U6: DRV8874PWPR; HTSSOP-16 PWP0016J; LCSC C1855818

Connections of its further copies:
+3.3V: C33.1, U6.5 (VREF), U6.16 (PMODE); also elsewhere on the board
+5V: C36.1, J11.3; also elsewhere on the board
+12V: C28.1, C29.2, C30.1, C31.1, U6.11 (VM); also elsewhere on the board
/LIFT2_HALL1: C37.1, R36.2; also elsewhere on the board
/LIFT2_HALL2: C35.1, R35.1; also elsewhere on the board
/LIFT2_IN1: U6.1 (EN/IN1); also elsewhere on the board
/LIFT2_IN2: U6.2 (PH/IN2); also elsewhere on the board
/lift2/CPH: C32.1, U6.13 (CPH)
/lift2/CPL: C32.2, U6.14 (CPL)
/lift2/IPROPI: C34.1, R37.1, U6.6 (IPROPI)
/lift2/OUT1: J11.5, U6.8 (OUT1)
/lift2/OUT2: J11.4, U6.10 (OUT2)
/lift2/VCP: C31.2, U6.12 (VCP)
/~LIFT_FAULT: U6.4 (~FAULT); also elsewhere on the board
/~LIFT_SLEEP: U6.3 (~SLEEP); also elsewhere on the board
GND: C28.2, C29.1, C30.2, C33.2, C34.2, C35.2, C36.2, C37.2, D7.3 (A), J11.2, R37.2, U6.9 (PGND), U6.15 (GND), U6.17 (PAD); also elsewhere on the board
unnamed: D7.2 (K), J11.1, R35.2
unnamed: D7.1 (K), J11.6, R36.1

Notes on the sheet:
CONNECTOR FOR PA-09 LINEAR ACTUATOR
PMODE set to use PWM mode via IN1 and IN2 IMODE set to fixed off-time current chopping, outputs latched off overcurrent response ~{SLEEP} enables driver when high ~{FAULT} is open-drain
LIFT ACTUATOR MOTOR DRIVER
CURRENT LIMIT
Designed for 12 V DC motor load up to 3 A (driver is rated for 6 A peak)
Set overcurrent protection trip current Itrip (A) = 450 * Vref (V) / Ripropi (Ω) Given Vref = 3.3 V, Ripropi = 470 Ω, Itrip = 3.16 A
The hall sensor outputs are push-pull at 5 V, RC filter cutoff at 15.9 kHz

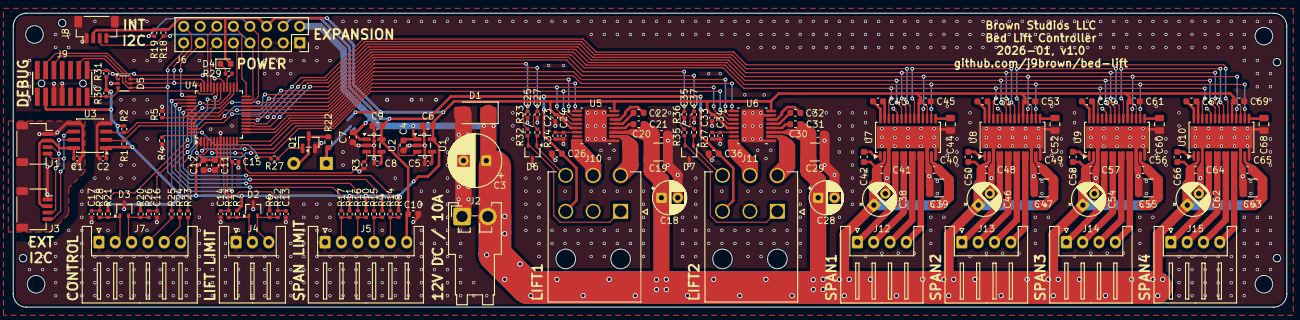
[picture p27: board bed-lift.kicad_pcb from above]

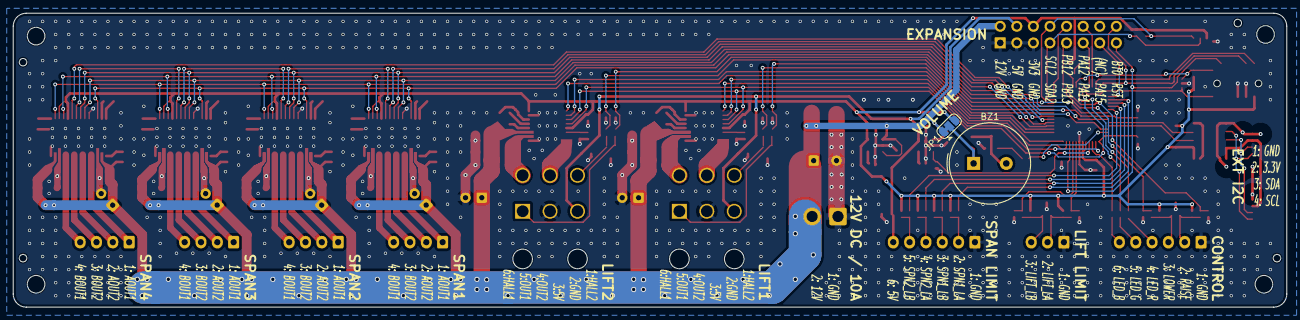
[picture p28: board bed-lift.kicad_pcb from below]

Board: 4 copper layers, 195.0 x 45.0 mm, 149 parts (2 on the bottom side), 121 nets.

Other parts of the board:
MP1, MP2, MP3, MP4: MountingHole_2.7mm_M2.5
TH1, TH1#2, TH1#3, TH1#4: JLCPCB_PCBA_Tooling_Hole

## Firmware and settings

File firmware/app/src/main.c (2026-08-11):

#include <zephyr/drivers/gpio.h>
#include <zephyr/drivers/watchdog.h>
#include <zephyr/kernel.h>
#include <zephyr/logging/log.h>

#include "bed/bed.h"
#include "bed/lift.h"
#include "bed/span.h"
#include "control.h"
#include "indicator.h"
#include "melody.h"
#include "monitor.h"
#include "power.h"

LOG_MODULE_REGISTER(app);

#define WATCHDOG_TIMEOUT_MS (1000)
static const struct device *watchdog_dev = DEVICE_DT_GET(DT_NODELABEL(iwdg));

// Timeout for the indicator to go dark after completing an activity.
#define ACTIVITY_TIMEOUT_MS (1500)

// Timeout to revert to the main menu after completing an activity.
#define MENU_TIMEOUT_MS (15000)

/*
 * Error codes.
 */

INDICATOR_PATTERN_LOOP(indicator_pattern_aborted, 0,
    INDICATOR_PATTERN_ENTRY(INDICATOR_HUE_AMBER, 2, 2, 1));

INDICATOR_PATTERN_LOOP(indicator_pattern_generic_error, 0,
    INDICATOR_PATTERN_ENTRY(INDICATOR_HUE_RED, 2, 2, 1));

INDICATOR_PATTERN_LOOP(indicator_pattern_control_error, 4,
    INDICATOR_PATTERN_ENTRY(INDICATOR_HUE_RED, 5, 3, 1),
    INDICATOR_PATTERN_ENTRY(INDICATOR_HUE_MAGENTA, 1, 3, INDICATOR_PATTERN_PARAM_CYCLES));

INDICATOR_PATTERN_LOOP(indicator_pattern_bed_error, 4,
    INDICATOR_PATTERN_ENTRY(INDICATOR_HUE_RED, 5, 3, 1),
    INDICATOR_PATTERN_ENTRY(INDICATOR_HUE_AMBER, 1, 3, INDICATOR_PATTERN_PARAM_CYCLES));

INDICATOR_PATTERN_LOOP(indicator_pattern_lift_error, 4,
    INDICATOR_PATTERN_ENTRY(INDICATOR_HUE_RED, 5, 3, 1),
    INDICATOR_PATTERN_ENTRY(INDICATOR_HUE_CYAN, 1, 3, INDICATOR_PATTERN_PARAM_CYCLES));

INDICATOR_PATTERN_LOOP(indicator_pattern_span_error, 4,
    INDICATOR_PATTERN_ENTRY(INDICATOR_HUE_RED, 5, 3, 1),
    INDICATOR_PATTERN_ENTRY(INDICATOR_HUE_BLUE, 1, 3, INDICATOR_PATTERN_PARAM_CYCLES));

static void show_error(int err) {
    switch (ERROR_CATEGORY(err)) {
        case ERROR_CATEGORY(CONTROL_ERROR_FIRST_):
            indicator_pattern(indicator_pattern_control_error, ERROR_INDEX(err));
            break;
        case ERROR_CATEGORY(BED_ERROR_FIRST_):
            indicator_pattern(indicator_pattern_bed_error, ERROR_INDEX(err));
            break;
        case ERROR_CATEGORY(LIFT_ERROR_FIRST_):
            indicator_pattern(indicator_pattern_lift_error, ERROR_INDEX(err));
            break;
        case ERROR_CATEGORY(SPAN_ERROR_FIRST_):
            indicator_pattern(indicator_pattern_span_error, ERROR_INDEX(err));
            break;
        default:
            indicator_pattern(indicator_pattern_generic_error, 0);
            break;
    }
}

/*
 * Melodies.
 */

MELODY(melody_error_forbidden,
    MELODY_NOTE(E6, 50), MELODY_REST(50), MELODY_NOTE(E6, 50), MELODY_REST(50), MELODY_NOTE(E6, 50));

MELODY(melody_error_alert,
    MELODY_NOTE(E6, 500), MELODY_REST(250), MELODY_NOTE(E6, 500), MELODY_REST(250), MELODY_NOTE(E6, 500));

MELODY(melody_pose_lounge,
    MELODY_NOTE(E6, 50), MELODY_REST(50), MELODY_NOTE(E6, 50), MELODY_REST(50), MELODY_NOTE(G6, 250));

MELODY(melody_pose_sleep,
    MELODY_NOTE(E6, 50), MELODY_REST(50), MELODY_NOTE(E6, 50), MELODY_REST(50), MELODY_NOTE(C6, 250));

MELODY(melody_menu_mode,
    MELODY_NOTE(E6, 50));

MELODY(melody_menu_main,
    MELODY_NOTE(E6, 50), MELODY_REST(25), MELODY_NOTE(F6, 25), MELODY_REST(25),
    MELODY_NOTE(E6, 25), MELODY_REST(25), MELODY_NOTE(D6, 25), MELODY_REST(25),
    MELODY_NOTE(E6, 50));

MELODY(melody_menu_jog_lift,
    MELODY_NOTE(E6, 50), MELODY_REST(50), MELODY_NOTE(F6, 50), MELODY_REST(50), MELODY_NOTE(G6, 50));

MELODY(melody_menu_jog_span,
    MELODY_NOTE(E6, 50), MELODY_REST(50), MELODY_NOTE(D6, 50), MELODY_REST(50), MELODY_NOTE(C6, 50));

static void melody_play_error(int err) {
    switch (err) {
        case CONTROL_ERROR_INHIBITED:
            melody_play(melody_error_forbidden);
            break;
        default:
            melody_play(melody_error_alert);
            break;
    }
}

static void melody_play_pose(void) {
    switch (bed_get_current_pose()) {
        case BED_POSE_LOUNGE:
            melody_play(melody_pose_lounge);
            break;
        case BED_POSE_SLEEP:
            melody_play(melody_pose_sleep);
            break;
        default:
            break;
    }
}

/*
 * Jog specifications.
 */

INDICATOR_PATTERN_LOOP(indicator_pattern_jog_lift, 4,
    INDICATOR_PATTERN_ENTRY(INDICATOR_HUE_AMBER, 5, 3, 1),
    INDICATOR_PATTERN_ENTRY(INDICATOR_HUE_CYAN, 1, 3, INDICATOR_PATTERN_PARAM_CYCLES));

struct jog_lift_spec {
    enum lift_move move;
    unsigned indicator_pattern_param;
};
static const struct jog_lift_spec jog_lift_specs[] = {
    { .move = LIFT_MOVE_TANDEM, .indicator_pattern_param = 1,  },
    { .move = LIFT_MOVE_INDEPENDENT_BOTH, .indicator_pattern_param = 2 },
    { .move = LIFT_MOVE_INDEPENDENT_1, .indicator_pattern_param = 3 },
    { .move = LIFT_MOVE_INDEPENDENT_2, .indicator_pattern_param = 4 },
};

INDICATOR_PATTERN_LOOP(indicator_pattern_jog_span, 4,
    INDICATOR_PATTERN_ENTRY(INDICATOR_HUE_AMBER, 5, 3, 1),
    INDICATOR_PATTERN_ENTRY(INDICATOR_HUE_BLUE, 1, 3, INDICATOR_PATTERN_PARAM_CYCLES));

struct jog_span_spec {
    enum span_move move;
    unsigned actuator_set;
    unsigned indicator_pattern_param;
};
static const struct jog_span_spec jog_span_specs[] = {
    { .move = SPAN_MOVE_HOME, .actuator_set = SPAN_ACTUATOR_SET_ALL, .indicator_pattern_param = 1 },
    { .move = SPAN_MOVE_HOME, .actuator_set = SPAN_ACTUATOR_SET_01, .indicator_pattern_param = 2 },
    { .move = SPAN_MOVE_HOME, .actuator_set = SPAN_ACTUATOR_SET_23, .indicator_pattern_param = 3 },
    { .move = SPAN_MOVE_JOG, .actuator_set = BIT(0), .indicator_pattern_param = 4 },
    { .move = SPAN_MOVE_JOG, .actuator_set = BIT(1), .indicator_pattern_param = 5 },
    { .move = SPAN_MOVE_JOG, .actuator_set = BIT(2), .indicator_pattern_param = 6 },
    { .move = SPAN_MOVE_JOG, .actuator_set = BIT(3), .indicator_pattern_param = 7 },
};

/*
 * Menus.
 */

enum menu {
    MENU_MAIN = 0,
    MENU_JOG_LIFT = 1,
    MENU_JOG_SPAN = 2,
};

struct menu_spec {
    const unsigned mode_count;
    const melody_t *melody;
};
static const struct menu_spec menu_specs[] = {
    { 0, melody_menu_main },
    { ARRAY_SIZE(jog_lift_specs), melody_menu_jog_lift },
    { ARRAY_SIZE(jog_span_specs), melody_menu_jog_span },
};

static enum menu menu;
static unsigned menu_mode;

/*
 * Control interface.
 */

static int do_rest(void) {
    return bed_poll_stop();
}

static void do_goto_menu(enum menu new_menu) {
    menu_mode = 0;
    if (menu != new_menu) {
        menu = new_menu;
        melody_play(menu_specs[menu].melody);
    }
}

static void do_next_menu(void) {
    do_goto_menu(menu + 1 >= ARRAY_SIZE(menu_specs) ? MENU_MAIN : menu + 1);
}

static void do_next_menu_mode(void) {
    const unsigned count = menu_specs[menu].mode_count;
    if (count) {
        menu_mode += 1;
        if (menu_mode >= count) {
            menu_mode = 0;
        }
        melody_play(melody_menu_mode);
    }
}

static int do_move(bool up, struct monitor_setting setting) {
    if (setting.control_inhibit) {
        return CONTROL_ERROR_INHIBITED;
    }
    switch (menu) {
        case MENU_MAIN:
            return bed_poll_pose(up ? BED_POSE_LOUNGE : BED_POSE_SLEEP);
        case MENU_JOG_LIFT: {
            bed_prepare_for_manual_action();
            int span_err = span_poll_sleep();
            int lift_err = lift_poll_jog(jog_lift_specs[menu_mode].move, up);
            return span_err ? span_err : lift_err;
        }
        case MENU_JOG_SPAN: {
            bed_prepare_for_manual_action();
            int span_err = span_poll_jog(jog_span_specs[menu_mode].move, up, jog_span_specs[menu_mode].actuator_set);
            int lift_err = lift_poll_sleep();
            return span_err ? span_err : lift_err;
        }
        default:
            return 0;
    }
}

static void show_status(void) {
    switch (menu) {
        case MENU_JOG_LIFT:
            indicator_pattern(indicator_pattern_jog_lift, 
                    jog_lift_specs[menu_mode].indicator_pattern_param);
            break;
        case MENU_JOG_SPAN:
            indicator_pattern(indicator_pattern_jog_span,
                    jog_span_specs[menu_mode].indicator_pattern_param);
            break;
        case MENU_MAIN:
        default:
            switch (bed_get_state()) {
                case BED_STATE_ERROR:
                    indicator_pattern(indicator_pattern_generic_error, 0);
                    break;
                case BED_STATE_ABORTED:
                    indicator_pattern(indicator_pattern_aborted, 0);
                    break;
                case BED_STATE_MOVING:
                    switch (bed_get_target_pose()) {
                        case BED_POSE_LOUNGE:
                            indicator_on(k_uptime_get() << 5);
                            break;
                        case BED_POSE_SLEEP:
                            indicator_on(-k_uptime_get() << 5);
                            break;
                        default:
                            __ASSERT(false, "");
                            break;
                    }
                    break;
                case BED_STATE_DONE:
                    indicator_on(INDICATOR_HUE_GREEN);
                    break;
            }
            break;
    }
}

static int setup(void) {
    int err;
    struct wdt_timeout_cfg watchdog_cfg = {
        .window = {
            .min = 0,
            .max = WATCHDOG_TIMEOUT_MS,
        },
        .callback = NULL,
        .flags = WDT_FLAG_RESET_SOC,
    };
    if ((err = wdt_install_timeout(watchdog_dev, &watchdog_cfg))) {
        return err;
    }
    if ((err = wdt_setup(watchdog_dev, WDT_OPT_PAUSE_HALTED_BY_DBG))) {
        return err;
    }
    if ((err = melody_init())) {
        return err;
    }
    if ((err = control_init())) {
        return err;
    }
    if ((err = monitor_init())) {
        return err;
    }
    if ((err = power_init())) {
        return err;
    }
    if ((err = bed_init())) {
        return err;
    }
    return 0;
}

enum command {
    COMMAND_NONE = 0,
    COMMAND_NEXT_MENU = 1,
    COMMAND_NEXT_MENU_MODE = 2,
    COMMAND_MOVE_UP = 3,
    COMMAND_MOVE_DOWN = 4,
    COMMAND_AUTO_MOVE_UP = 5,
    COMMAND_AUTO_MOVE_DOWN = 6,
};

static void loop(void) {
    static int last_error;

    static enum command command_previous;
    static bool command_issued;   // true if the command has been issued, result indicates most recent status
    static int command_result;    // 0 means done (ready to rest), 1 means in progress (issue again), < 0 means error (abort)
    static int64_t command_time;  // time when the command was last issued
    static enum control_action control_action_previous;

    // Determine which command to perform based on control inputs.
    enum control_action control_action_next = control_get_action();
    enum command command_next;
    switch (control_action_next) {
        case CONTROL_ACTION_HOLD_UP:
            command_next = COMMAND_MOVE_UP;
            break;
        case CONTROL_ACTION_HOLD_UP_THEN_PRESS_MODE:
            command_next = COMMAND_AUTO_MOVE_UP;
            break;
        case CONTROL_ACTION_HOLD_DOWN:
            command_next = COMMAND_MOVE_DOWN;
            break;
        case CONTROL_ACTION_HOLD_DOWN_THEN_PRESS_MODE:
            command_next = COMMAND_AUTO_MOVE_DOWN;
            break;
        case CONTROL_ACTION_HOLD_MODE:
            command_next = menu != MENU_MAIN ? COMMAND_NEXT_MENU : COMMAND_NONE;
            break;
        case CONTROL_ACTION_LONG_HOLD_MODE:
            command_next = menu == MENU_MAIN ? COMMAND_NEXT_MENU : COMMAND_NONE;
            break;
        case CONTROL_ACTION_RELEASE:
            switch (control_action_previous) {
                case CONTROL_ACTION_PRESS_MODE:
                    command_next = COMMAND_NEXT_MENU_MODE;
                    break;
                default:
                    if ((command_previous == COMMAND_AUTO_MOVE_UP || command_previous == COMMAND_AUTO_MOVE_DOWN)
                            && command_issued && command_result == 1) {
                        command_next = command_previous;
                    } else {
                        command_next = COMMAND_NONE;
                    }
                    break;
            }
            break;
        default:
            command_next = COMMAND_NONE;
            break;
    }
    control_action_previous = control_action_next;
    command_previous = command_next;
    LOG_DBG("Loop control %d, command %d, menu %d, menu mode %d", control_action_next, command_next, menu, menu_mode);

    // Invoke the command.
    const struct monitor_setting setting = monitor_get_setting();
    bool did_move = false;
    if (command_next == COMMAND_NONE) {
        command_issued = false;
        command_result = 0;
    } else if (!command_issued || command_result == 1) {
        command_issued = true;
        command_time = k_uptime_get();
        command_result = 0;
        switch (command_next) {
            case COMMAND_MOVE_UP:
            case COMMAND_AUTO_MOVE_UP:
                command_result = do_move(/*up*/ true, setting);
                did_move = true;
                break;
            case COMMAND_MOVE_DOWN:
            case COMMAND_AUTO_MOVE_DOWN:
                command_result = do_move(/*up*/ false, setting);
                did_move = true;
                break;
            case COMMAND_NEXT_MENU:
                do_next_menu();
                break;
            case COMMAND_NEXT_MENU_MODE:
                do_next_menu_mode();
                break;
            default:
                break;
        }
    }
    if (!command_issued || command_result <= 0) {
        int err = do_rest();
        if (!command_result) {
            command_result = err;
        }
    }
    static int log_err_command_result;
    static enum command log_err_command_next;
    if (log_err_command_result != command_result || log_err_command_next != command_next) {
        log_err_command_result = command_result;
        log_err_command_next = command_next;
        if (command_result < 0) {
            LOG_ERR("Error %d from command %d", log_err_command_result, log_err_command_next);
        }
    }

    if (command_result < 0) {
        melody_play_error(command_result);
        last_error = command_result;
    } else if (did_move && menu == MENU_MAIN && command_result == 0) {
        melody_play_pose();
    }

    // Update menu.
    if (menu != MENU_MAIN && k_uptime_get() - command_time >= MENU_TIMEOUT_MS) {
        do_goto_menu(MENU_MAIN);
    }
    if (menu != MENU_MAIN) {
        // Enable 5V power so the span hall sensors operate while on the test menu.
        power_5v_request(POWER_DEMAND_TEST);
    } else {
        power_5v_release(POWER_DEMAND_TEST);
    }

    // Update indicators.
    if (command_result < 0) {
        show_error(command_result);
    } else if (k_uptime_get() - command_time < ACTIVITY_TIMEOUT_MS
            || menu != MENU_MAIN) {
        show_status();
    } else {
        indicator_pattern(NULL, 0);
    }

    // Update monitor status.
    struct monitor_status status = {
        .bed_state = bed_get_state(),
        .bed_pose_current = bed_get_current_pose(),
        .bed_pose_target = bed_get_target_pose(),
        .lift_position = lift_get_position(),
        .lift_state = lift_get_state(),
        .span_position = span_get_position(),
        .span_state = span_get_state(),
        .control_inhibited = setting.control_inhibit,
        .control_active = command_issued,
        .control_error = !!command_result,
        .last_error = -last_error,
    };
    monitor_set_status(status);
}

int main(void) {
    int err;
    if ((err = setup())) {
        indicator_on(INDICATOR_HUE_RED);
        return err;
    }

    while (true) {
        if ((err = wdt_feed(watchdog_dev, 0))) {
            return err;
        }
        loop();
        k_msleep(10);
    }
    return 0;
}

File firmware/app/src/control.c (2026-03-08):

#include <errno.h>
#include <zephyr/drivers/gpio.h>
#include <zephyr/kernel.h>
#include <zephyr/sys/atomic.h>

#include "control.h"

#define ZEPHYR_USER_NODE DT_PATH(zephyr_user)
static const struct gpio_dt_spec control_up_gpio = GPIO_DT_SPEC_GET(ZEPHYR_USER_NODE, control_up_gpios);
static const struct gpio_dt_spec control_down_gpio = GPIO_DT_SPEC_GET(ZEPHYR_USER_NODE, control_down_gpios);

#define CONTROL_DEBOUNCE_MS (10)
#define CONTROL_HOLD_MS (500)
#define CONTROL_LONG_HOLD_MS (3000 - CONTROL_HOLD_MS)

static struct gpio_callback control_gpio_callback;

static atomic_t control_action_pending;
static atomic_t control_action_current;

static void control_work_handler(struct k_work* work);
K_WORK_DELAYABLE_DEFINE(control_work, control_work_handler);

static void control_gpio_handler(const struct device *port, struct gpio_callback *cb, gpio_port_pins_t pins) {
    gpio_port_value_t value = 0;
    gpio_port_get(port, &value);
    bool control_up = IS_BIT_SET(value, control_up_gpio.pin);
    bool control_down = IS_BIT_SET(value, control_down_gpio.pin);
    enum control_action action;
    if (control_up && !control_down) {
        action = CONTROL_ACTION_PRESS_UP;
    } else if (control_down && !control_up) {
        action = CONTROL_ACTION_PRESS_DOWN;
    } else if (control_up && control_down) {
        action = CONTROL_ACTION_PRESS_MODE;
    } else {
        action = CONTROL_ACTION_RELEASE;
    }
    atomic_set(&control_action_pending, action);
    k_work_reschedule(&control_work, K_MSEC(CONTROL_DEBOUNCE_MS));
}

static void control_work_handler(struct k_work* work) {
    enum control_action pending = atomic_get(&control_action_pending);
    enum control_action current = atomic_get(&control_action_current);
    bool reschedule_for_hold;
    k_timeout_t hold_time;
    switch (pending) {
        case CONTROL_ACTION_PRESS_UP:
            if (current == CONTROL_ACTION_HOLD_UP_THEN_PRESS_MODE) {
                return; // no change
            }
            reschedule_for_hold = atomic_cas(&control_action_pending, pending, CONTROL_ACTION_HOLD_UP);
            hold_time = K_MSEC(CONTROL_HOLD_MS);
            break;
        case CONTROL_ACTION_PRESS_DOWN:
            if (current == CONTROL_ACTION_HOLD_DOWN_THEN_PRESS_MODE) {
                return; // no change
            }
            reschedule_for_hold = atomic_cas(&control_action_pending, pending, CONTROL_ACTION_HOLD_DOWN);
            hold_time = K_MSEC(CONTROL_HOLD_MS);
            break;
        case CONTROL_ACTION_PRESS_MODE: {
            enum control_action current = atomic_get(&control_action_current);
            switch (current) {
                case CONTROL_ACTION_HOLD_UP:
                    pending = CONTROL_ACTION_HOLD_UP_THEN_PRESS_MODE;
                    reschedule_for_hold = false;
                    break;
                case CONTROL_ACTION_HOLD_DOWN:
                    pending = CONTROL_ACTION_HOLD_DOWN_THEN_PRESS_MODE;
                    reschedule_for_hold = false;
                    break;
                case CONTROL_ACTION_HOLD_UP_THEN_PRESS_MODE:
                case CONTROL_ACTION_HOLD_DOWN_THEN_PRESS_MODE:
                    return; // no change
                default:
                    reschedule_for_hold = atomic_cas(&control_action_pending, pending, CONTROL_ACTION_HOLD_MODE);
                    hold_time = K_MSEC(CONTROL_HOLD_MS);
                    break;
            }
            break;
        }
        case CONTROL_ACTION_HOLD_MODE:
            reschedule_for_hold = atomic_cas(&control_action_pending, pending, CONTROL_ACTION_LONG_HOLD_MODE);
            hold_time = K_MSEC(CONTROL_LONG_HOLD_MS);
            break;
        default:
            reschedule_for_hold = false;
            hold_time = K_MSEC(0);
            break;
    }
    if (reschedule_for_hold) {
        k_work_reschedule(&control_work, hold_time);
    }

    atomic_set(&control_action_current, pending);
}

int control_init(void) {
    int err;
    const struct device *port = control_up_gpio.port;
    if (port != control_down_gpio.port) {
        return -EIO;
    }
    if (!device_is_ready(port)) {
        return -ENODEV;
    }
    gpio_init_callback(&control_gpio_callback, control_gpio_handler,
        BIT(control_up_gpio.pin) | BIT(control_down_gpio.pin));

    if ((err = gpio_pin_configure_dt(&control_up_gpio, GPIO_INPUT)) ||
            (err = gpio_pin_configure_dt(&control_down_gpio, GPIO_INPUT))) {
        return err;
    }
    if ((err = gpio_pin_interrupt_configure_dt(&control_up_gpio, GPIO_INT_EDGE_BOTH)) ||
            (err = gpio_pin_interrupt_configure_dt(&control_down_gpio, GPIO_INT_EDGE_BOTH))) {
        return err;
    }
    if ((err = gpio_add_callback(port, &control_gpio_callback))) {
        return err;
    }
    return 0;
}

enum control_action control_get_action(void) {
    return atomic_get(&control_action_current);
}

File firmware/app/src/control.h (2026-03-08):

/**
 * @file
 * @brief Reads the control button state.
 */

#pragma once

#include <stdint.h>

enum control_action {
    CONTROL_ACTION_RELEASE = 0,
    CONTROL_ACTION_PRESS_UP = 1,
    CONTROL_ACTION_PRESS_DOWN = 2,
    CONTROL_ACTION_PRESS_MODE = 3,
    CONTROL_ACTION_HOLD_UP = 4,
    CONTROL_ACTION_HOLD_DOWN = 5,
    CONTROL_ACTION_HOLD_MODE = 6,
    CONTROL_ACTION_HOLD_UP_THEN_PRESS_MODE = 7,
    CONTROL_ACTION_HOLD_DOWN_THEN_PRESS_MODE = 8,
    CONTROL_ACTION_LONG_HOLD_MODE = 9,
};

/**
 * @brief Get the action determined by the buttons.
 */
enum control_action control_get_action(void);

/**
 * @brief Initialize the control driver.
 */
int control_init(void);

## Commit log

2025-10-15 Import the v0.1 hardware and firmware.
    [bed-lift.kicad_pcb, bed-lift.kicad_sch, linear-actuator-driver.kicad_sch]
2025-10-22 First draft of the new bed lift PCB.
    [bed-lift.kicad_pcb, bed-lift.kicad_sch, lift.kicad_sch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]
2025-10-22 Finalize for production
    [bed-lift.kicad_pcb, bed-lift.kicad_sch, lift.kicad_sch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]
2025-11-03 Create v0.3 hardware from v0.2.
    [bed-lift.kicad_pcb, bed-lift.kicad_sch, lift.kicad_sch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]
2025-11-04 Update v0.3 to address errata.
    Moved the board design and errata into a versioned documents.
    Added some photos of the bed.
    [bed-lift.kicad_pcb, bed-lift.kicad_sch, lift.kicad_sch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]
2025-11-04 Clarify the workaround for the motor connector mismatch.
2025-11-19 Add todo for more capacitors
2025-12-02 Implement the span movement loop as high prority thread.
2025-12-03 Variable step frequency and stall learning.
    Stall detection does not work because there is too much jitter between
    steps issued over SPI. So this code will need to be rewritten to output
    steps with a hardware GPIO.
    [drv8434s.c, drv8434s.h, span.c]
2025-12-07 Rewrite step sequencer using PWM for accurate timing.
    Stall detection works now and the acoustics are much better.
    [control.c, control.h, drv8434s.c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]
2025-12-07 Amend errata for timer pins.
2025-12-08 Disable the fault interrupt handler.
    Avoid sharing the EXTI line with a different GPIO that's more important.
    Reduce code size.
    [drv8434s.c, drv8434s.h, span.c]
2025-12-16 Implement the rest of the lift functionality.
    Implemented a PID control loop for the linear actuators.
    Improved error reporting.
    Resolved issues with the linear actuator hall sensors.
    [control.c, control.h, drv8434s.c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]
2025-12-17 Add an external monitoring interface over I2C.
    Enabled LTO to reduce flash size.
    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
    [errors.h, indicator.c, lift.c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]
2025-12-22 Tuning and integration.
    Set stall threshold dynamically based on the speed of travel.
    Filter out brief stalls when the mechanism binds slightly.
    Allow individual span actuators to be disabled, span 1 is currently intermittent.
    Reduce the span actuator speed at the start and end of travel.
    Use slow decay during PWM to improve lift actuator torque and prevent
    voltage spikes.
    [drv8434s.c, drv8434s.h, errors.h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]
2025-12-30 Perform a simple rainbow color wheel progress animation.
    Showing the actual progress as a color wasn't effective.
2026-01-04 Complete first draft of v1.0 hardware.
    [bed-lift.kicad_pcb, bed-lift.kicad_sch, lift.kicad_sch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]
2026-01-04 Review BOM.
    [bed-lift.kicad_pcb, bed-lift.kicad_sch]
2026-01-06 Improve power distribution.
    [bed-lift.kicad_pcb, bed-lift.kicad_sch, lift.kicad_sch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]
2026-01-14 Further refinement, ready for fabrication.
    [bed-lift.kicad_pcb, bed-lift.kicad_sch, lift.kicad_sch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]
2026-01-14 Move new bed-lift hardware to v1 folder.
    Minor revisions will be performed in-situ without duplicating everything.
    [bed-lift.kicad_pcb, bed-lift.kicad_sch, lift.kicad_sch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]
2026-01-15 Correct the BOOT0 pin polarity in the documentation.
    [bed-lift.kicad_sch]
2026-01-15 Finalize for production of v1.0 revision.
    [bed-lift.kicad_pcb, bed-lift.kicad_sch, lift.kicad_sch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]
2026-01-30 Prepare for development of the v1 firmware.
    Rearranged the project as a Zephyr West style workspace to be compatible
    with the latest version of Zephyr. Unfortunately Platform IO does not
    support building Zephyr 4.3 projects right now and we need the latest
    board files for the STM32C051.
    Deleted the v0.1 firmware altogether.
2026-02-01 Update firmware for v1 hardware.
    Updated pin assignments
    Decoupled lift and span sleep state.
    Added control of 5 V regulator.
    Added on-board "power" indicator.
    Added audible feedback.
    Enabled timer break function to stop lift immediately on faults.
    Added logging support, optional and controlled by build flags
    Added more monitoring diagnostics over I2C.
    Added a span test mode for tuning stall detection.
    Significantly increased the speed of travel of the spans.
    Fixed hiccup when lift exits safe zone before span ends travel.
    Added span hall sensor reading.
    [errors.h, indicator.c, lift.c]
2026-02-02 Enable span limit sensors and reduce speed during partial travel.
2026-02-03 Improve documentation, rearrange error codes.
    [errors.h]
2026-03-08 Improve bed travel parameters for reliability.
2026-03-08 Add a mode to lock the lift into automatic movement.
    Rewrote the command dispatch to enable new features.
    Lengthened the time that the mode button must be held to access
    diagnostic modes to lessen the likelihood of accidental entry.
    Added a tone to facilitate blind menu navigation.
